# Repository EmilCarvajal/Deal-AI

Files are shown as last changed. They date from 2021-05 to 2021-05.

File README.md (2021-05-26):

# [ROBOTICA] Deal-AI
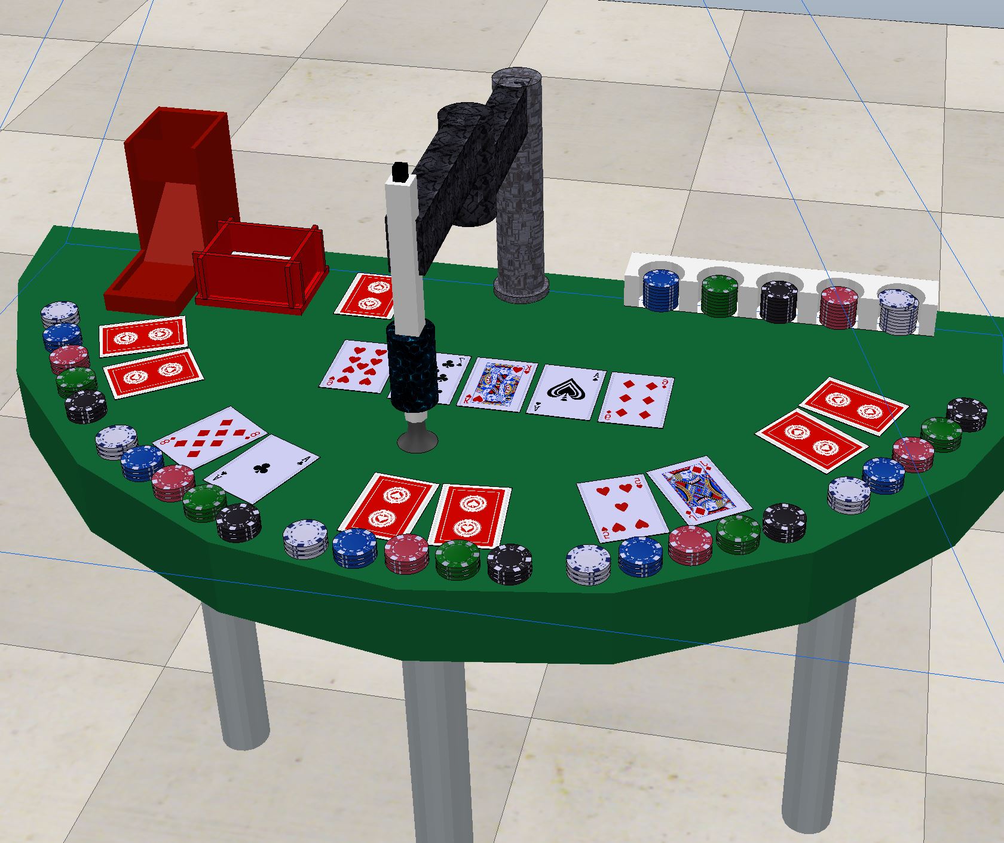
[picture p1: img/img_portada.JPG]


Brazo mecánico que  permite actuar como  Dealer o Croupier en el juego del  Poker, concretamente la modalidad de Texas Holdem.
También ayuda a controlar el estado de la partida.

# Tabla de Contenidos
* [Descripción de proyecto](#descripción-del-proyecto)

* [Amazing contributions](#amazing-contributions)

* [Esquema Hardware](#esquema-hardware)	

* [Piezas 3D](#piezas-3d)

* [Arquitectura software](#arquitectura-software)

* [Módulos](#módulos)
  * [Módulo de Jugadores](#módulo-de-jugadores)  <br>
  * [Módulo de cinemática inversa](#módulo-de-cinemática-inversa)  <br>
  * [Módulo de visión por computador](#módulo-de-visión-por-computador)  <br> 
       * [Detección de cartas](#detección-de-cartas)  <br>
       * [Detección de fichas](#detección-de-fichas)  <br>
  * [Módulo de inteligencia artificial](#módulo-de-inteligencia-artificial) <br>
       * [Main](#main) <br>
       * [Módulo de cambio](#módulo-de-cambio) <br>
* [Vídeo](#vídeo)

* [Autores](#autores)

# Descripción del proyecto	
DEAL_AI es un robot que ayuda a dirigir el estado de una partida del clásico juego de cartas Poker actuando como Dealer o Croupier.
Básicamente consiste en un brazo mecánico de 4 ejes con la misma estructura de un robot SCARA que tiene acoplada una ventosa para poder distribuir las fichas y las cartas que están en juego. Este robot está diseñado para una mesa semicircular la cual está adaptada a su zona de trabajo.  Existe un componente situado al lado de la base el cual le permite girar las cartas simplemente soltándolas por encima del objeto. Para reconocer las fichas y las cartas tiene una cámara colocada en una torre central elevada.
Sus principales funciones son:
*	Funciones de Dealer: 
       *	Flop (mostrar las 3 cartas)
       * Mostar las 5 cartas
       * Voltear cartas
       *	Repartir cartas 
*	Intercambio de fichas mediante IA
*	Realizar movimientos y responder preguntas (órdenes captadas por reconocimiento de voz)
* Declarar ganador por medio de visión por computador.

# Amazing contributions
Gracias a su adaptación para permitir cualquier número de jugadores, DEAL_AI puede ser utilizado en partidas amateurs o en partidas profesionales.
En cuanto a las partidas amistosas o hechas por principiantes, el robot permite a los jugadores tener una mayor comprensión del juego gracias a su seguimiento por comandos de voz y a su automatización en el intercambio de fichas. 
Para los jugadores profesionales, es ideal tener un crupier robótico, pues uno de los mayores problemas en el póker es la realización de [trampas](https://www.pokernews.com/news/2020/05/the-muck-bill-perkins-dan-cates-alleged-cheating-37330.htm) en medio de la partida. Se han dado casos donde el jugador que repartía cartas (en caso de no haber crupier) realizaba trampas para manipular las cartas que recibía cada jugador y, en otras ocasiones, un jugador estaba [compinchado con el crupier](https://www.straitstimes.com/singapore/courts-crime/rws-casino-croupier-and-patron-charged-with-cheating), por tanto este manipulaba las cartas que repartía a cada jugador.
Además, gracias a su movilidad automatizada y adaptable a las circunstancias de la partida, DEAL_AI tiene acceso a todos los rincones de la zona de juego, así pues en mesas grandes donde un jugador debe realizar un esfurezo físico para alcanzar la zona, lo que puede suponer un problema sobretodo para gente mayor, con discapacidad o problemas físicos, el robot es capaz de alcanzar las cartas y las fichas de cada jugador, ahorrandoles este esfuerzo inecesario para disfrutar de la partida de póker.

# Esquema Hardware
El proyecto en cuestión roza los 100€ de presupuesto con componentes de media calidad. Es necesario que 3 de los servo-motores sean capaces de realizar una rotación de 360º. Cabe destacar que, cuanto mayor sea la definición de la cámara, más se reducirá la tasa de error del robot al realizar la detección de fichas y, sobretodo, de cartas: Recomendamos una cámara capaz de grabar en Full HD.

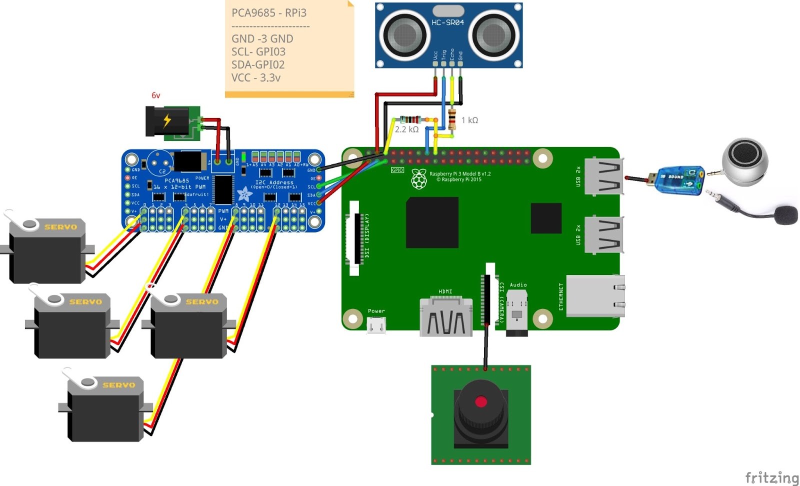
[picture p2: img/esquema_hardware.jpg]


# Piezas 3D
Para la realización de este proyecto, se han utilizado las siguientes piezas 3D:

**Componentes unidos del brazo robótico (total de 4 piezas por separado).**
<br>
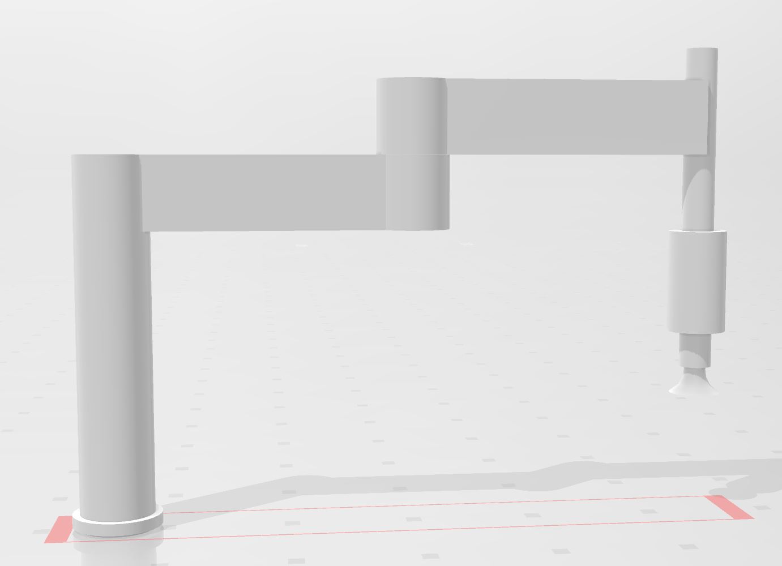
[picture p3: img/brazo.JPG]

<br>
<br>

**Base personalizada para colocar la baraja de cartas.**
<br>
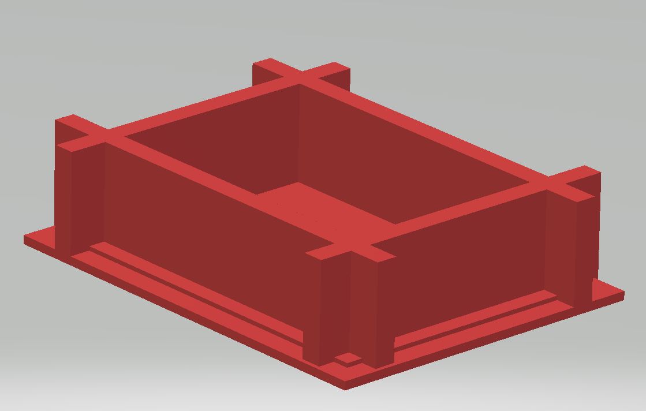
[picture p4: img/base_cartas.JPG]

<br>
<br>

**Pieza que permite al robot voltear las cartas.**
<br>
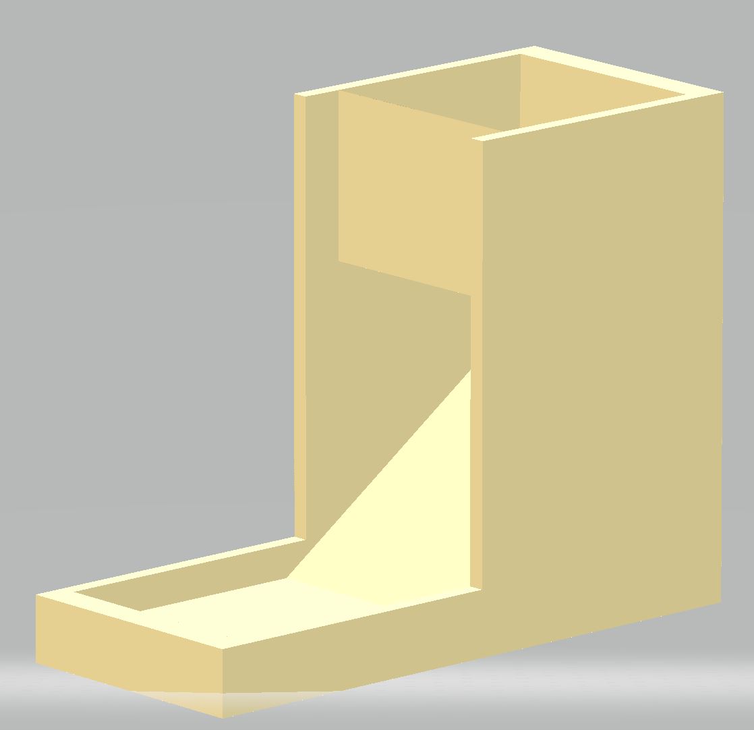
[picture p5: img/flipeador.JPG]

<br>
<br>

**Mesa semicircular utilizada en el simulador como zona de juego (no se ha de imprimir en caso de realizarlo en la vida real).**
<br>
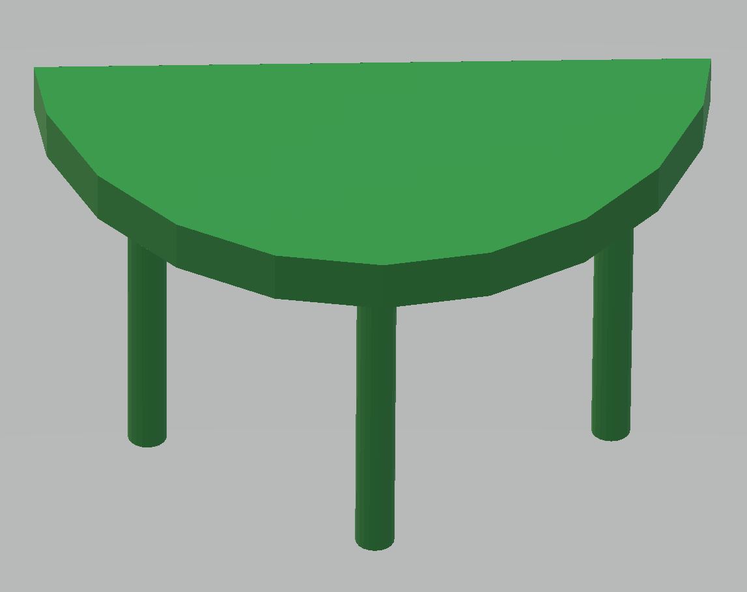
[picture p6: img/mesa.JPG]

<br>
<br>
Todas y cada una de estas piezas se encuentran en la carpeta **Objetos STL** de este mismo repositorio. No obstante, las dimensiones de los objetos NO SON CORRECTAS, simplemente conservan las buenas proporciones y relaciones de tamaño, pero en caso de querer utilizarlos se ha de tener en cuenta que se han de escalar al tamaño deseado. En nuestro caso, al utilizar un simulador y trasladarlo todo a centímetros (por temas de capacidad de ejecución y limitación de los própios ordenadores), se han escalado la gran mayoría de piezas a un ratio de entre 0.001 y 0.01 de su tamaño original.

# Arquitectura software
Destacamos un total de 4 módulos imprescindibles en este proyecto los cuales, al sincronizarse, permiten al robot realizar un seguimiento eficiente de la partida de póker que se esté llevando a cabo. Dichos módulos son:
* Módulo de jugadores: Reconocimiento de comandos de voz (inputs) que permiten al robot poder avanzar en la partida o la acción a realizar en cada momento. También permite a los jugadores consultar dudas básicas que tengan.
* Módulo de cinemática inversa: Movimiento absoluto del robot, ya sea para repartir cartas, intercambiar fichas o dar la vuelta a las cartas. Este módulo en particular también permite la reorientación correcta de las cartas.
* Módulo de visión por computador: Reconocimiento de fichas y cartas. Es capaz de detectar el valor de las fichas estándar de póker (colores blanco, azul, verde, rojo, negro) y el valor y palo de las cartas.
* Módulo de inteligencia artificial: Representa el cerebro del robot, el cual recibe los inputs de los demás módulos y genera los outputs que necesitan los demás módulos.
* Controladores: Estos relacionan los demás módulos entre si y permiten una perfecta sincronización entre ellos para poder efectuar las acciones necesarias.

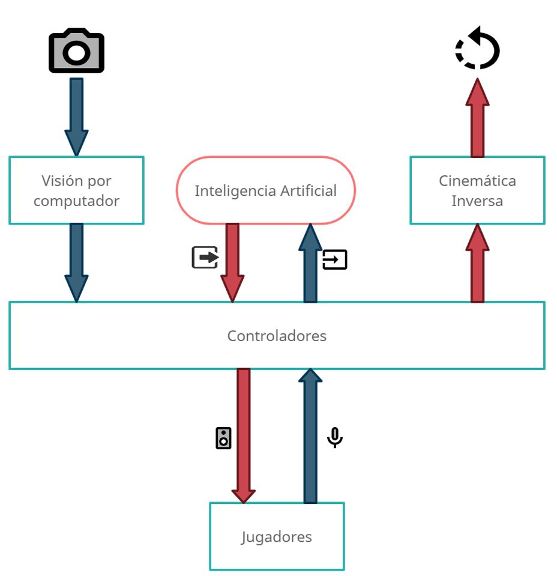
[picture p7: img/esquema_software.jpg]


# Módulos
## Módulo de jugadores
Representa el colectivo de seres humanos que están realizando una partida con el Deal AI. Estos son los que generarán los inputs principales, los cuales permitirán determinar al robot qué algoritmo utilizar y con qué módulos operar.

Para poder permitir esta interacción entre el boto y los jugadores, se han utilizado los módulos/librerías:
* speech_recognition (para el reconocimiento de voz, así dando la oportunidad de controlar las acciones del robot). 
> pip install SpeechRecognition
* gTTS (para poder leer con voz sintética (text-to-speech) las respuestas dadas por el robot)
> pip install gTTS
* playsound (para poder reproducir sonidos y poder leer los resultados obtenidos por el gTTS).
> pip install playsound

## Módulo de cinemática inversa
En este módulo se aplicará a los servo-motores los ángulos calculados para permitir al robot alcanzar el objeto o la posición deseada rotando sus ejes principales. Básicamente tras haber establecido la posición (módulo IA) el controlador ordenará a los componentes hardware la cinemática a realizar.

Lo principal para poder empezar a desplazar nuestro robot hacia las posiciones deseadas, es calcular las ecuaciones de movimiento del robot mediante una tabla de Denavit Hartenberg (tabla de D-H).

Para ello, hacemos los correspondientes cálculos en función de la diferencia entre las distancias y orientaciones de un servo-motor y otro. Al aplicar los cálculos correctos, obtenemos la siguiente matriz resultante para el cálculo de la cinemática inversa de un robot SCARA de 4 ejes:  

header pic

En esta ecuación conocemos los valores de la, lb, lc y l4 que equivalen a la distancia de cada brazo o link. Los datos que desconocemos son ϑ1, ϑ2, ϑ4 y d3, que equivaldrían a los ángulos de rotación de los servo-motores 1, 2 y 4 (los cuales son rotacionales) y la altura a la que está situada el manipulador (controlado por el servo-motor 3 que es de tipo prismático). Para saber qué rotación hay que aplicar a cada eje, utilizamos la última columna para realizar un sistema de ecuaciones que, al resolverlo, nos determinará las rotaciones a aplicar en cada eje. No obstante, si queremos saber la rotación correspondiente para punto geométrico (x, y, z), debemos restar estos valores a su ecuación correspondiente (la primera fila corresponde a la 'x', la segunda a la 'y' y la tercera a la 'z').

En nuestro caso utilizamos la librería sympy.
> import sympy as sp  
> from sympy import *

Dicha librería nos permite obtener una representación más visual de las ecuaciones y utilizar funciones de resolución de sistemas de ecuaciones para encontrar las incógnitas. En nuestro caso, mediante la matriz de DH mostrada previamente:
> nsolve(matrix, (theta1,theta2,d3,theta4),(1, 1, 1, 1))

Para facilitar la faena de los programadores, se crean módulos estándar que serán utilizados en las funciones principales, así pues, para repartir cartas a un jugador, en vez de reescribir el código de cinemática inversa, se utiliza un módulo de movimiento estándar que es llamado por la función de mayor nivel.

Con este sistema establecido, generamos las siguientes funciones de alto nivel:

*	**PosicionJugador(nJugadores):** Se pasa como parámetro ‘nJugadores’ que corresponde al número de participantes que jugarán a póker. La función calcula y devuelve las posiciones geométricas de cada jugador y el ángulo correspondiente (entre 90 y -90 grados porque es una mesa semicircular y el robot está orientado en el ángulo 0 grados).

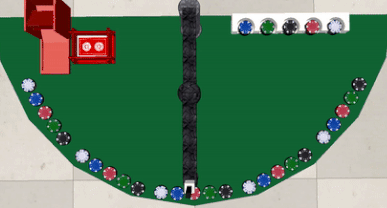
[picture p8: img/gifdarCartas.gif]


*	**DarCartaJugador(x, y, angulo):** Se pasa como parámetro la posición central de un jugador. En esta función se le suma y resta a esta posición un coeficiente pequeño que determina la separación entre una carta y otra, pues en esta modalidad de póker ser reparten dos cartas a cada jugador. Una vez aplicado este cálculo, se determina de la posición central un total de 2 posiciones, que equivalen a las posiciones de cada carta. Puesto que se colocan las cartas de los jugadores en el perímetro del área, al colocar el eje rotacional en el ángulo 0 grados, las cartas quedan orientadas apuntando hacia el centro de la mesa.

*	**RevelarCartasCentrales():** En esta función se revelan las cartas correspondientes cuando da inicio una nueva ronda. En esta modalidad de póker, se revelan un total de 5 cartas: 3 cartas en la primera ronda, 1 carta en la segunda y 1 carta en la tercera.

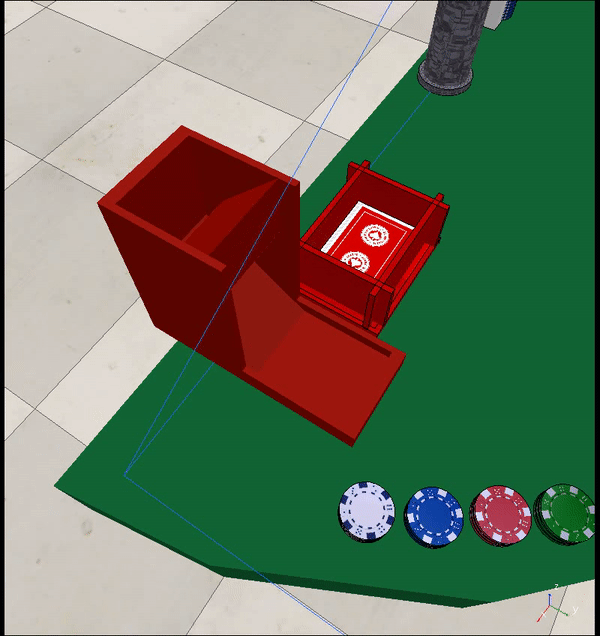
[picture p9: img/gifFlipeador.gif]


* **Ir_a_flipeador():** Tras analizar y probar varios modelos de piezas 3D que permitan voltear una carta automáticamente, hemos encontrado la pieza necesaria para lograrlo. Tras situar la pieza en un lugar específico de la zona de juego, el brazo robótico únicamente debe colocar encima de la pieza la carta que desea voltear, rotando dicha carta para que quepa en la entrada y se voltee automáticamente, deslizándose hasta una pequeña zona donde se recogerá la carta.

*	**QuemarCarta():** En muchos juegos de cartas de apuestas antes de repartir cartas o de revelar cartas se realiza una acción denominada como “quemar carta” que simplemente consta en coger la primera carta del mazo y colocarla en una pila de descartes.

**Problema 1:** La función ‘nsolve’ muestra problemas para encontrar el camino óptimo que ha de recorrer el robot y, en ciertas ocasiones para llegar a la coordenada de destino realiza más vueltas de las necesarias (gira más de 360 grados).

**Solución 1:** En el módulo del cálculo de la cinemática inversa se aplica el módulo a la solución para así obtener un resultado entre 0 y 360 grados:

> angulo=angulo % 2π

En este caso, ‘angulo’ es el parámetro que nos devuelve la función ‘nsolve’ que equivaldría a la rotación que debería ejercer el servo-motor para alcanzar la coordenada en cuestión. 2π equivale a 360 grados en radianes.

**Problema derivado 1.1:** La operación módulo (%) no tiene en cuenta el signo del ángulo, es decir, si la variable ‘angulo’ es positiva, el resultado será positivo, pero en caso de ser un valor negativo, el resultado que devuelve es positivo cosa que no nos interesa, pues hay una gran diferencia entre girar 45 y -45 grados.

**Solución 1.1:** Puesto que no hay ninguna función que permita realizar la operación de módulo devolviendo el signo correcto, se detecta el signo antes de aplicar la operación y, en caso de ser negativo, se calcula el módulo con el valor positivo y luego se negativiza el resultado.

**Problema derivado 1.2:** La variable ‘angulo’ ahora está comprendida entre 0 y 360 grados, pero en ciertas ocasiones el brazo gira casi 360 grados para acceder a una posición cercana si se desplazara en dirección contraria. Por ejemplo, si el robot quiere situarse en el centro del 4to cuadrante (cuadrante (x, -y) entre los ángulos 270 y 360) podría acceder de manera rápida si rotara -45 grados, pero la función nos devuelve un valor de 315, por tanto el brazo rota un total de 315 grados lo cual no es óptimo.

**Solución 1.2:** Los brazos robóticos con capacidad de rotación de 360 grados pueden dividirse en dos zonas de movimiento óptimo: de 0 a 180 grados y de 0 a -180 grados (que equivaldría a la zona comprendida entre 180 y 360 grados). Si el robot quiere rotar 181 grados, es más eficaz que rote -179 grados, pues llegará a la misma posición rotando menos grados. Por tanto, se determina un condicional que si detecta que la variable ‘angulo’ supera los 180 grados (que en radianes equivale a π), entonces se le resta 360 grados a ‘angulo’ (equivalente a 2π), así pues, en el mismo caso de antes, si tenemos 181 grados y le restamos 360, obtenemos -179 que sería nuestro ángulo óptimo.

**Solución final:** Juntando todas estas soluciones, obtenemos un módulo capaz de corregir cualquier ángulo y transformarlo en uno óptimo (si es que no lo era antes):

Cuanto a los módulos de bajo nivel, mencionamos algunos que creemos que son interesantes mencionar:
* **CogerItem():** Activa la válvula de vacío.
* **CogerCarta():** Automatiza la acción de coger una carta de la baraja (utilizando la función CogerItem()).
* **DejarItem():** Desactiva la válvula de vacío.

## Módulo de visión por computador:
Entendemos este módulo como el que recoge la información de la situación en la zona de juego. Dicha información se utilizará posteriormente para poder establecer las posiciones de los elementos a manipular por el robot (cartas y fichas) y para que pueda determinar la situación en tiempo real de la partida (reconocimiento de las cartas).

Finalmente, para este módulo se ha decidido hacerlo junto con el proyecto final de la asignatura “Visión por Computador”. El robot será capaz de detectar tanto cartas como fichas. Además de detectarlos podrá saber sus valores concretos.

### Detección de cartas
Se ha limitado una zona para cada jugador donde se encontrarán las cartas y fichas correspondientes de cada jugador. Se ha implementado una función llamada “**detectarCartes()**” que se le pasan por parámetro la región de la imagen del jugador recortada y otra igual pero binarizada (en blanco y negro) y la cantidad de cartas que se esperan que se detecten (2 si son la de los jugadores y 5 si son las de la máquina). Esta función se encarga de tractar las imágenes que recibe para devolver 3 vectores, el primero contiene una imagen de cada carta, el segundo una imagen del rango / valor de las cartas detectadas (A, 1, 2, 3, …, Q,K) y el tercero contiene una imagen del palo de cada carta detectada (corazón, picas, tréboles, rombos).  
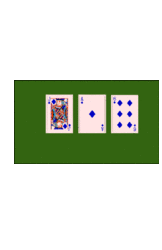
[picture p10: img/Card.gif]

También, se ha implementado una función llamada “**detectarValors()**” que recibe las imágenes de los valores y tipos obtenidos en la función “**detectarCartes()**” y un dataset de valores de cartas y un dataset de valores de palos de Póker. En esta función se usan los dataset que se pasan por parámetro para clasificar los palos y valores de cada una de las imágenes que también recibe y devolver 2 vectores en un formato específico para posteriormente determinar quién es el ganador.  
Para poder saber quién es el ganador, se ha implementado una función llamada “**comboJugador()**” que mediante los vectores que devuelve “**detectarValors()**” le da una puntuación al jugador sobre la mano que tiene y con qué combo (pareja, doble pareja, escalera, …) ha obtenido esa puntuación (el jugador que obtenga la mayor puntuación será el ganador).

### Detección de fichas
Para esta detección, no se utilizan las mismas zonas que para las cartas porque estas no coinciden con la zona natural donde un jugador podría dejar sus fichas (entendemos que un jugador no situaría las fichas que quiere cambiar encima de sus cartas sino un poco más alejado de ellas). Así pues, antes de que el robot las detecte, sume su valor y pueda recogerlas y llevarlas a la banca de fichas para su intercambio, lo primero que se ha realizar es determinar las áreas de cambio.  
Se ha creado la función "**valorFichas(img_Robot)**" que se encarga de determinar el valor de una ficha. Esta recibe una imagen de la área determinada por el jugador que pide cambio de fichas. La imagen contiene varias fichas, pero al estar apiladas solo ve la que está más por encima.
Los pasos que emplea son:
*	Eliminación del ruido 
*	Encuentra el área del fondo 
*	Encuentra el área segura que pertenece a la ficha
*	Encuentra la región desconocida (bordes)
*	Etiquetado de las manchas que detecta
*	Adiciona 1 a todas las etiquetas para asegurra que el fondo sea 1 en lugar de cero
*	Se marca la región desconocida con ceros
*	Utiliza técnica “watershed” para dividir las manchas
*	Se binariza la imagen
*	Buscamos los contornos las manchas restantes con la función cv2.findContours()
*	Recortamos la mancha
*	Le añadimos brillo mediante la función increase_brightness()
*	Realizamos una media de pixeles y vemos que color es más cercano para asociarle

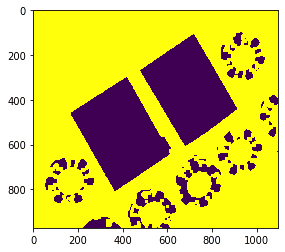
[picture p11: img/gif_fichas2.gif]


## Módulo de inteligencia artificial
### Main
Este es el núcleo del robot, donde todos los inputs son transmitidos a este módulo el cual se encargará de dar una serie de órdenes al robot. Estas órdenes pasarán por su controlador en concreto y establecerá una acción: o bien utilizará el altavoz para dar un mensaje a los jugadores o bien realizará un movimiento para alcanzar una posición calculada previamente.

Este main representa el sistema del juego Póker en la modalidad Texas Holdem pero con ciertos cambios que permiten que se adapte a una partida cotidiana entre amigos.
Por eso, cada jugador empieza con una cantidad de fichas determinadas. El sistema está organizado por “Manos” y “Rondas”. Denominamos Manos a 4 Rondas completas donde en la última se decide quién es el jugador que ha ganado la Mano y se lleva todo el dinero situado en el bote. Un Ronda es terminada cuando todos los jugadores activos de la Mano han apostado la misma cantidad de fichas. En la Ronda 0 se reparten las cartas y se realizan las apuestas iniciales, en la Ronda 1 se colocan 3 cartas centrales en la mesa y en la ronda 2 y 3 se “quema” una carta y se coloca otra junto a las centrales. “Quemar” una carta no es más que coger una carta y descartarla colocándola en una pila de descartes.
El sistema controla la secuencia de juego y mantiene el estado de los jugadores que no se han retirado para pasar a la siguiente ronda. 
Controla en todo momento los jugadores que están activos y los que han abandonado la mesa (no se contemplan para las siguientes Manos y no se les reparte cartas).

Cuando es el turno de un jugador se le pregunta, por comandos de voz, qué acción desea realizar. Solo se ejecutan las acciones que ordena si se encuentran en el sistema. Estas acciones son típicas del juego como:
*	<ins> “Paso”:</ins> el jugador no desea subir la apuesta.
*	<ins> “Subo”:</ins> el jugador sube la apuesta y se reinicia el estado de los jugadores para confirmar sus nuevas acciones.
*	<ins> “Igualo, Voy”:</ins>  el jugador sigue la apuesta máxima y coloca sus fichas en la mesa.
*	<ins> “Me retiro”:</ins> Se retira de la Mano y no se le preguntará nada hasta la próxima Mano.
*	<ins> “Abandono”:</ins> Abandona la mesa y ya no se le tendrá en cuenta en las próximas Manos.
*	<ins> “Cambio a la alta/baja”:</ins> El jugador coloca sus fichas en su área de cambio según si desea cambio a valores altos o bajos. Implementado por el Módulo de Cambio.
*	<ins> Preguntas de estado:</ins>  Se le puede preguntar al sistema información sobre el estado del juego. Ej: “Dealer actual?”, “Ronda actual?, “Quién es la ciega grande?”, “Apuesta máxima?”… 

Cuando se ha llegado a la última Ronda de una Mano el sistema dice a los jugadores que han permanecido al final de la Mano que muestren sus cartas. 
El sistema reconoce todas las cartas que hay en la mesa gracias al módulo de visión por computador y determina el jugador que ha ganado y la combinación de cartas con lo que lo ha hecho. 

Para las siguientes Manos el sistema de juego es el mismo. Se termina el juego cuando solo queda un jugador en la mesa.

### Módulo de cambio
Este módulo controla el sistema de cambio de fichas. Se implementa en 3 etapas: reconocimiento de las fichas que se desean cambiar y llevarlas a la banca, tratamiento del valor total de las fichas para establecer cuantas monedas y de qué tipo ha de devolver y por último la secuencia de movimientos para colocar las fichas de cambio.

Funciones:
*	**recogerFichasMonton(area):** Por medio de un área establecida controla el módulo de visión por computador de las fichas para poder reconocerlas y luego a través de las funciones de cinemática inversa coloca esas fichas en su determinada posición de la banca.

*	**cambiar_fichas_greedy(suma_fichas,mode):** Algoritmo greedy (sacado  de la asignatura de la mención “Analisis y disseny d’algortimes” ) implementado para saber qué fichas ha de devolver el robot. Implementa 2 modos para devolver fichas con valores bajos o máximos.

*	**dar_Cambio(cambio, posicion):** Recibe qué fichas se han de devolver y la matriz de la posición donde el jugador dejó sus fichas de cambio.

# Vídeo
Haz click para ver el video:
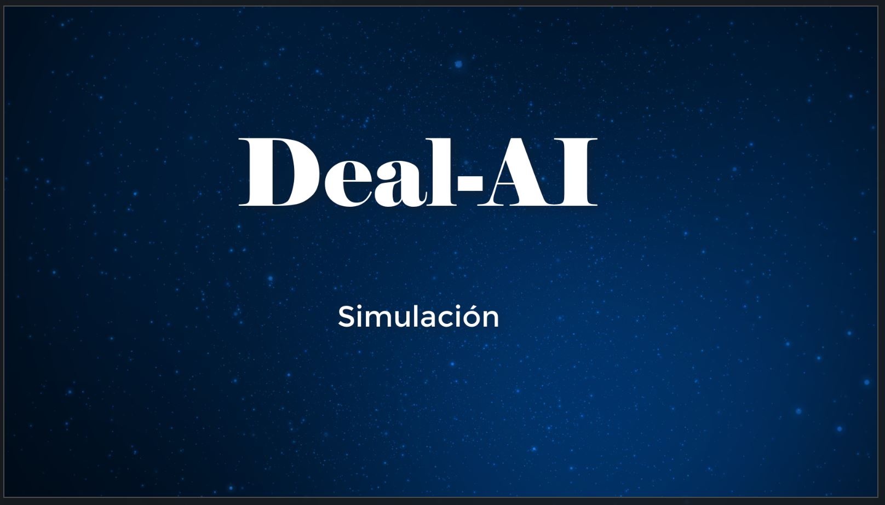
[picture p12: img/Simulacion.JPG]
Watch the video (https://www.youtube.com/watch?v=U3uC58L_5Mo&ab_channel=Emilsj2)


# Autores
Emil Carvajal - 1529821   
Marc Gordón - 1457460   
Jofre Gómez - 1526889   
Denís Montoya - 1527418

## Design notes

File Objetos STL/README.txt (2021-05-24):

Los objetos siguen las proporciones adecuadas, pero NO ESTÁN ESCALADOS al 
tamaño correcto, por tanto consultar proporciones si se quieren implementar.

Objetos como las cartas o las fichas son para representar la forma, el valor
de cada uno se representará después individualmente. En caso de usar Coppelia
se aplicará una 'Quick Texture' para añadir el valor de la ficha o de la carta.

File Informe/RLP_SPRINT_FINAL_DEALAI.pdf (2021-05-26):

RPL - Computer Engineering. UAB (Barcelona) 2020-2021

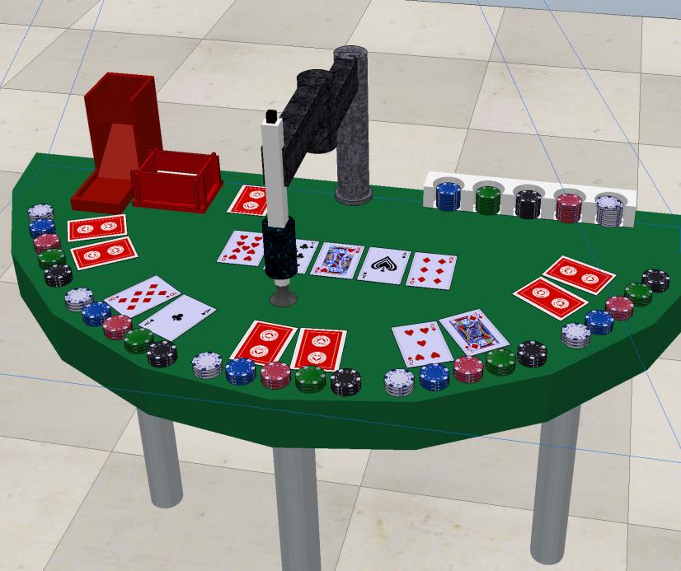
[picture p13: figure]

# DEAL_AI

Brazo | mecánico | que | permite actuar como
Dealer o Croupier | en | el | juego del | Poker,
concretamente la modalidad de Texas Holdem. También ayuda a controlar el estado de la partida.

PROJECT SPRINT #5.
DATE: 25th May 2021

EMIL CARVAJAL 1529821 #1
DENÍS MONTOYA 1527418 #2
MARC GORDÓN 1457460 #3
JOFRE GÓMEZ 1526889 #4

DEAL_AI

## Tabla de contenido

Sprint #5
Date: 25 Mayo 2021
DEAL_AI | 1

## DEAL_AI

Brazo mecánico que permite actuar como Dealer o Croupier en el juego del Poker, concretamente la modalidad de Texas Holdem. También ayuda a controlar el estado de la partida.

Descripción del Proyecto

DEAL_AI es un robot que ayuda a dirigir el estado de una partida del clásico juego de cartas Poker actuando como Dealer o Croupier.

Básicamente consiste en un brazo mecánico de 4 ejes con la misma estructura de un robot SCARA que tiene acoplada una ventosa para poder distribuir las fichas y las cartas que están en juego. Este robot está diseñado para una mesa semicircular la cual está adaptada a su zona de trabajo. Existe un componente situado al lado de la base el cual le permite girar las cartas simplemente soltándolas por encima del objeto. Para reconocer las fichas y las cartas tiene una cámara colocada en una torre central elevada.

Sus principales funciones son:

- Funciones de Dealer:
- Flop (mostrar las 3 cartas)
- Mostar las 5 cartas
- Quemar cartas
- Incluye voltear las cartas
- Repartir Cartas
- Intercambio de fichas mediante IA
- Realizar movimientos y responder preguntas (órdenes captadas por reconocimiento de voz)
- Declarar ganador por medio de visión por computador.

DEAL_AI | 2

Componentes electrónicos

■ Placa PCA9685

■ Raspberry pi 3

■ 4 Servomotores

■ Cámara

■ Adaptador de audio

■ Micrófono

■ Altavoz

■ Ventosa de bomba de aire de vacío

■ 5 sensores de ultrasonido

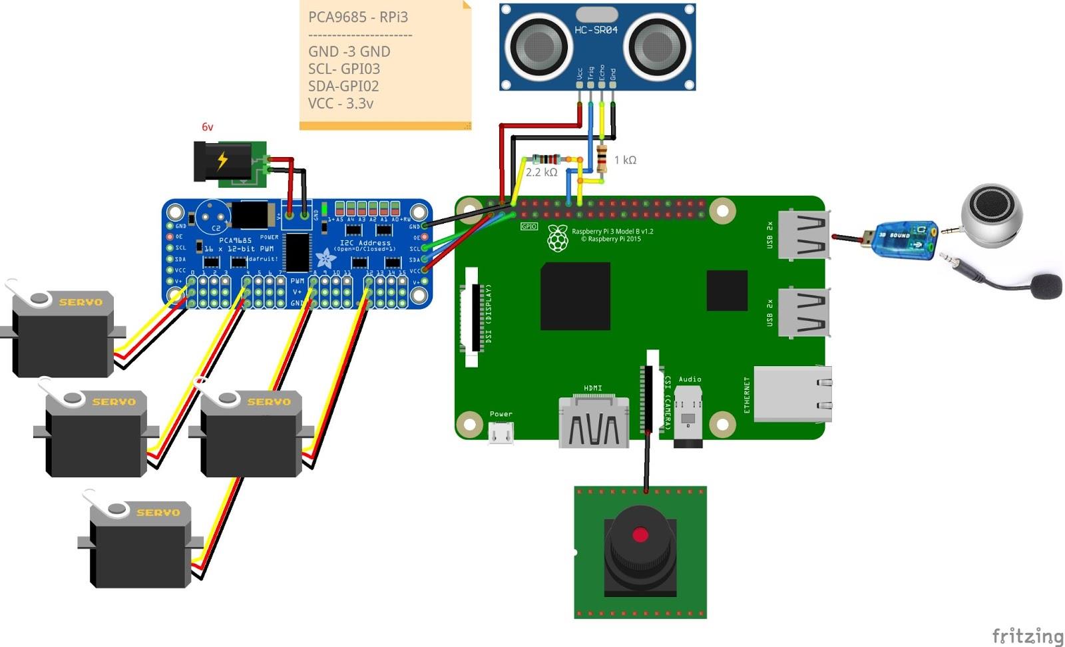
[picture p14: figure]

DEAL_AI | 3

Esquema Hardware

CONEXIONES (--> Serie // Paralelo)

SERVO1,2,3,4 (pin,v,gnd) --> PCA9685 ( (0,4,8,12 ) , 5v, GND) )

PCA9685 (Vin,GND,SCL,SDA) --> Raspberry pi 3 (5v, GND, GIPO03,GIPO04)

Raspberry pi 3 (CSI camera) --> Camera

Raspberry pi 3 ( USB1 port) --> Adaptador de Audio

Adaptador de Audio( in ) --> External Microphone

Adaptador de Audio( out ) --> External Speaker

HC - SR04 (Vcc,GND,Trig,Echo) --> Raspberry pi 3 (5v, GND, (GND,GIPO23), GIPO24)

- | HC - SR04 (Trig) --> R1(1kΩ) --> | Raspberry pi 3(GIPO24)
// R2(2.2kΩ) --> | Raspberry pi 3(GND)

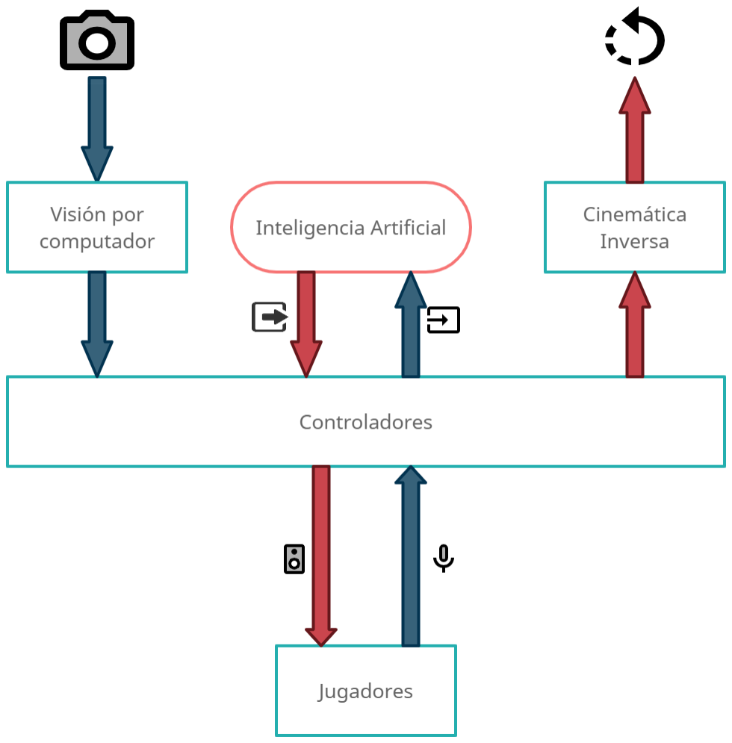
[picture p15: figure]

DEAL_AI | 4

Arquitectura Software

DEAL_AI | 5

Visión por computador:

Entendemos este módulo como el que recoge la información de la situación en la zona de juego. Dicha información se utilizará posteriormente para poder establecer las posiciones de los elementos a manipular por el robot (cartas y fichas) y para que pueda determinar la situación en tiempo real de la partida (reconocimiento de las cartas).

Finalmente, para este módulo se ha decidido hacerlo junto con el proyecto final de la asignatura “Visión por Computador”. El robot será capaz de detectar tanto cartas como fichas. Además de detectarlos podrá saber sus valores concretos.

Para la detección de cartas, se ha limitado una zona para cada jugador conde se encontrarán las cartas y fichas correspondientes de cada jugador.
Se ha implementado una función llamada “detectarCartes” que se le pasan por parámetro la región de la imagen del jugador recortada y otra igual pero binarizada (en blanco y negro) y la cantidad de cartas que se esperan que se detecten (2 si son la de los jugadores y 5 si son las de la máquina). Esta función se encarga de tractar las imágenes que recibe para devolver 3 arrays, el 1º contiene una imagen de cada carta, el 2º una imagen del rango / valor de las cartas detectadas (A, 1, 2, 3, …, Q,K) y el 3º contiene una imagen del palo de cada carta detectada (corazón, picas, tréboles, rombos).
También, se ha implementado una función llamada “detectarValors” que recibe las imágenes de los valores y tipos obtenidos en la función “detectarCartes” y un dataset de valores de cartas y un dataset de valores de palos de Poker. En esta función se usan los dataset que se pasan por parámetro para clasificar los palos y valores de cada una de las imágenes que también recibe y devolver 2 arrays en un formato específico para posteriormente determinar quien es el ganador. Para poder saber quien es el ganador, se ha implementado una función llamada “comboJugador” que mediante los arrays que devuelve “detectarValors” le da una puntuación al jugador sobre la mano que tiene y con que combo (pareja, doble pareja, escalera, …) ha obtenido esa puntuación (el jugador que obtenga la mayor puntuación será el ganador).

DEAL_AI | 6

Para la detección de las fichas no se utilizan las mismas zonas que para las cartas porques estas no son usadas ya que no contienen el area donde el jugador puede dejar sus fichas para que el robot las detecte, sume su valor y pueda recogerlas y llevarlas a la banca de fichas para su intercambio. Por lo que lo primero ha sido determinar esas áreas de cambio

valorFichas(img_Robot): Función que se encarga de determinar el valor de una ficha. Esta recibe una imagen de la área determinada por el jugador que pide cambio de fichas. La imagen contiene varias fichas, pero al estar apiladas solo ve la que está más por encima.

Los pasos que emplea son:

- Eliminación del ruido
- Encuentra el área del fondo
- Encuentra el área segura que pertenece a la ficha
- Encuentra la región desconocida (bordes)
- Etiquetado de las manchas que detecta
- Adiciona 1 a todas las etiquetas para asegurra que el fondo sea 1 en lugar de cero
- Se marca la región desconocida con ceros
- Utiliza técnica “watershed” para dividir las manchas
- Se binariza la imagen
- Buscamos los contornos las manchas restantes con la función cv2.findContours()
- Recortamos la mancha
- Le añadimos brillo mediante la función increase_brightness()
- Realizamos una media de pixeles y vemos que color es más cercano para asociarle

### Cinemática inversa:

En este módulo se aplicará a los servo motores la cinemática inversa calculada para permitir al robot alcanzar el objeto o la posición deseada. Básicamente tras haber establecido la posición (módulo IA) el controlador ordenará a los componentes hardware la cinemática a realizar.

Lo principal para poder empezar a desplazar nuestro robot hacia las posiciones deseadas, es calcular las ecuaciones de movimiento del robot mediante una tabla de Denavit Hartenberg (tabla de D-H).

Para ello, hacemos los correspondientes cálculos en función de la diferencia entre las distancias y orientaciones de un servo-motor y otro. Al aplicar los cálculos correctos, obtenemos la siguiente matriz resultante para la cinemática inversa de un robot SCARA de 4 ejes:

En esta ecuación conocemos los valores de la, lb, lc y l4 que equivalen a la distancia de cada brazo o link. Los datos que desconocemos son ϑ1, ϑ2, ϑ4 y d3, que equivaldrían a los ángulos de rotación de los servo-motores 1, 2 y 4 (los cuales son rotacionales) y la altura a la que está situada el manipulador (controlado por el servo-motor 3 que es de tipo prismático). Así pues, programamos un módulo básico para el cálculo de estas coordenadas:

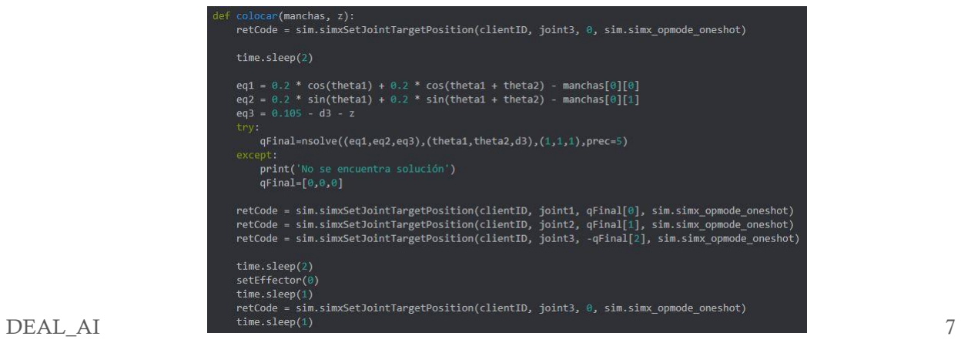
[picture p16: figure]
DEAL_AI

DEAL_AI | 8

Se utiliza el módulo base de la función “colocar” para ejercer toda la cinemática del robot. El núcleo de esta es la función “nsolve” que encontrar las incógnitas de un sistema de ecuaciones. Tanto las incógnitas como las ecuaciones se pasan como parámetros. En nuestro caso, se pasa como ecuaciones los resultados de aplicar la tabla D-H en un robot de 4 ejes SCARA y, para el movimiento, se encuentran los ángulos de los ejes rotacionales de los 2 primeros servo-motores. La altura no obstante será determinada mediante un sensor de ultrasonido, capaz de determinar la distancia a la que se encuentra la válvula de vacío (manipulador del robot) del objeto en cuestión (cartas o fichas).

Problema: La orientación del robot no es la predefinida, el robot está orientado en el eje de ordenadas en vez del de abscisas.

Solución: Se invierten los ejes en el cálculo de la posición, así pues, nuestras coordenadas realmente son (y, x).

Para facilitar la faena de los programadores, se crean módulos estándar que serán utilizados en las funciones principales, así pues, para repartir cartas a un jugador, en vez de reescribir el código de la cinemática inversa, se utiliza un módulo de movimiento estándar que es llamado por la función de mayor nivel.

Solución: Al utilizar un sistema de jerarquía de funciones, podemos volver a trabajar con el sistema de coordenadas (x,y) en general, hemos realizado el cambio a (y,x) en la función de menor nivel pero nos permite trabajar de manera normal y cómoda de esta forma.

Con este sistema establecido, generamos las siguientes funciones de alto nivel:

- PosicionJugador(nJugadores): | Se | pasa | como | parámetro
‘nJugadores’ que corresponde al número de participantes que jugarán a póker. La función calcula y devuelve las posiciones geométricas de cada jugador y el ángulo correspondiente (entre 90 y -90 grados porque es una mesa semicircular y el robot está orientado en el ángulo 0 grados).

DEAL_AI | 9
- DarCartaJugador(x, y, angulo): Se pasa como parámetro la posición central de un jugador. En esta función se le suma y resta a esta posición un coeficiente pequeño que determina la separación entre una carta y otra, pues en esta modalidad de póker ser reparten dos cartas a cada jugador. Una vez aplicado este cálculo, se determina de la posición central un total de 2 posiciones, que equivalen a las posiciones de cada carta. Puesto que se colocan las cartas de los jugadores en el perímetro del área, al colocar el eje rotacional en el ángulo 0 grados, las cartas quedan orientadas apuntando hacia el centro de la mesa.
- RevelarCartasCentrales(): En esta función se revelan las cartas correspondientes cuando da inicio una nueva ronda. En esta modalidad de póker, se revelan un total de 5 cartas: 3 cartas en la primera ronda, 1 carta en la segunda y 1 carta en la tercera.
- Ir_a_flipeador(): Tras analizar y probar varios modelos de piezas 3D que permitan voltear una carta automáticamente, hemos encontrado la pieza necesaria para lograrlo. Tras situar la pieza en un lugar específico de la zona de juego, el brazo robótico únicamente debe colocar encima de la pieza la carta que desea voltear, rotando dicha carta para que quepa en la entrada y se voltee automáticamente, deslizándose hasta una pequeña zona donde se recogerá la carta.

Problema: El brazo no es capaz de elevarse lo suficientemente alto como para colocar la carta en la parte superior de la pieza 3D.

Solución: Se han modificado las distintas dimensiones del robot, en concreto se ha incrementado la altura de la base del robot y se ha elevado el eje prismático, permitiéndonos depositar la carta en la parte superior del volteador.

Problema derivado: En algunos casos, para repartir las cartas a algunos jugadores, el brazo colisiona con el volteador de cartas, bloqueando el único medio de acceso hacia la posición del jugador.

Solución: Se ha modificado la función de nivel bajo CogerCarta() la cual, al recoger la carta de la baraja, la eleva lo máximo posible.

DEAL_AI | 10

De este modo, cada vez que se quiere acceder a una posición problemática, el brazo robótico se desplazará por encima de la pieza 3D, evitando colisiones innecesarias y permitiendo alcanzar cualquier posición sin impedimentos .

- QuemarCarta(): En muchos juegos de cartas de apuestas antes de repartir cartas o de revelar cartas se realiza una acción denominada como “quemar carta” que simplemente consta en coger la primera carta del mazo y colocarla en una pila de descartes.

Problema 1: La función ‘nsolve’ muestra problemas para encontrar el camino óptimo que ha de recorrer el robot y, en ciertas ocasiones para llegar a la coordenada de destino realiza más vueltas de las necesarias (gira más de 360 grados).

Solución 1: En el módulo del cálculo de la cinemática inversa se aplica el módulo a la solución para así obtener un resultado entre 0 y 360 grados:

angulo = angulo % 2π

En este caso, ‘angulo’ es el parámetro que nos devuelve la función ‘nsolve’ que equivaldría a la rotación que debería ejercer el servo-motor para alcanzar la coordenada en cuestión. 2π equivale a 360 grados en radianes.

Problema derivado 1.1: La operación módulo (%) no tiene en cuenta el signo del ángulo, es decir, si la variable ‘angulo’ es positiva, el resultado será positivo, pero en caso de ser un valor negativo, el resultado que devuelve es positivo cosa que no nos interesa, pues hay una gran diferencia entre girar 45 y -45 grados.

Solución 1.1: Puesto que no hay ninguna función que permita realizar la operación de módulo devolviendo el signo correcto, se detecta el signo antes de aplicar la operación y, en caso de ser negativo, se calcula el módulo con el valor positivo y luego se negativiza el resultado.

Problema derivado 1.2: La variable ‘angulo’ ahora está comprendida entre 0 y 360 grados, pero en ciertas ocasiones el brazo gira casi 360 grados para acceder

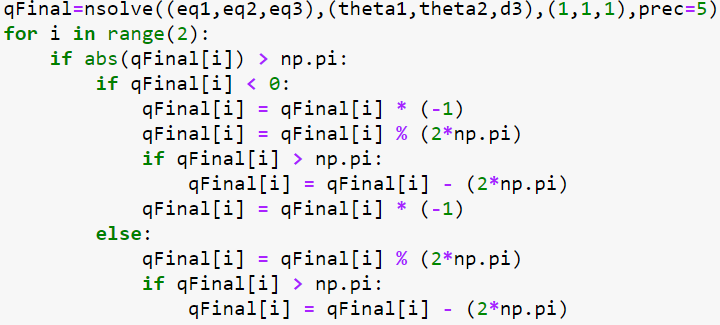
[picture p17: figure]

DEAL_AI | 11

a una posición cercana si se desplazara en dirección contraria. Por ejemplo, si el robot quiere situarse en el centro del 4to cuadrante (cuadrante (x, -y) entre los ángulos 270 y 360) podría acceder de manera rápida si rotara -45 grados, pero la función nos devuelve un valor de 315, por tanto, el brazo rota un total de 315 grados lo cual no es óptimo.

Solución 1.2: Los brazos robóticos con capacidad de rotación de 360 grados pueden dividirse en dos zonas de movimiento óptimo: de 0 a 180 grados y de 0 a -180 grados (que equivaldría a la zona comprendida entre 180 y 360 grados). Si el robot quiere rotar 181 grados, es más eficaz que rote -179 grados, pues llegará a la misma posición rotando una cantidad más pequeña de grados. Por tanto, se determina un condicional que si detecta que la variable ‘angulo’ supera los 180 grados (que en radianes equivale a π), entonces se le resta 360 grados a ‘angulo’ (equivalente a 2π), así pues, con el mismo caso de antes, si tenemos 181 grados y le restamos 360, obtenemos -179 que sería nuestro recorrido óptimo.

Solución final: Juntando todas estas soluciones, obtenemos un módulo capaz de corregir cualquier ángulo y transformarlo en uno óptimo (si es que no lo era antes):

Ejemplos de módulos de bajo nivel sería CogerItem() que activa la válvula de vacío, CogerCarta() que automatiza la acción de coger una carta de la baraja (utilizando la función CogerItem() ), DejarItem() que desactiva la válvula de

DEAL_AI | 12

vacío… En general son funciones sencillas que son llamadas varias veces por los módulos de alto nivel.

DEAL_AI | 13

Inteligencia Artificial:

Main:

Este es el núcleo del robot, donde todos los inputs son transmitidos a este módulo el cual se encargará de dar una serie de órdenes al robot. Estas órdenes pasarán por el controlador en concreto y establecerá una acción: o bien utilizará el altavoz para dar un mensaje a los jugadores o bien realizará un movimiento para alcanzar una posición calculada previamente.

Este main representa el sistema del juego Poker en la modalidad Holdem Texas pero con ciertos cambios que se adaptan a una partida cotidiana entre amigos. Por eso, cada jugador empieza con una cantidad de fichas determinadas. El sistema esta organizado por “Manos” y “Rondas”. Denominamos Manos a 4 Rondas completas donde en la última se decide quien es el jugador que ha ganado la Mano y se lleva todo el dinero invertido. Una Ronda es terminada cuando todos los jugadores activos de la Mano han apostado la misma cantidad de fichas. En la Ronda 0 se reparten las cartas, en la Ronda 1 se colocan 3 cartas centrales en la mesa y en la Ronda 2 i 3 se “quema” una carta y se coloca otra junto a las centrales. “Quemar” una carta no es más que coger una carta y descartar-la colocándola en una posición de la mesa.

El sistema controla la secuencia de juego y mantiene un estado de los jugadores que no se han retirado para pasar a la siguiente ronda.
Controla en todo momento los jugadores que están activos y los que han abandonado la mesa (no se contemplan para las siguientes Manos y no se les reparte cartas).

Cuando es el turno de un jugador se le pregunta, por comandos de voz, què acción desea realizar. Solo se ejecutan las acciones que ordena si se encuentran en el sistema. Estas acciones son típicas del juego como:
- “Paso”: el jugador no desea subir la apuesta.
- “Igualo, Voy”: el jugador sigue la apuesta máxima y coloca sus fichas en la mesa.
- “Me retiro”: Se retira de la Mano y no se le preguntará nada hasta la próxima Mano.

DEAL_AI | 14
- “Abandono”: Abandona la mesa y ya no se le tendrá más cuenta en el juego.
- “Cambio a la alta/baja”: El jugador coloca sus fichas en su área de cambio según si desea cambio a valores altos o bajos. Implementado por el Modulo de Cambio.
- Preguntas de estado: Se le puede preguntar al sistema información sobre el estado del juego:
Ej: “Dealer actual?”, “Ronda actual?, “Quién es la ciega grande?”, “Apuesta máxima?”…

Cuando se ha llegado a la última Ronda de una Mano el sistema dice a los jugadores que han permanecido al final de la Mano que muestren sus cartas. El sistema reconoce todas las cartas que hay en la mesa gracias al módulo de visión por computador y determina el jugador que ha ganado y la combinación de cartas con lo que lo ha hecho.

Para las siguientes Manos el sistema de juego es el mismo. Se termina el juego cuando solo queda un jugador en la mesa.

DEAL_AI | 15

Módulo de cambio:

Módulo que controla el sistema de cambio de fichas. Se implementa en 3 etapas: reconocimiento de las fichas que se desean cambiar y llevarlas a la banca, tratamiento del valor total de las fichas para establecer cuantas monedas y de qué tipo ha de devolver y por último la secuencia de movimientos para colocar las fichas de cambio.

Funciones:
- recogerFichasMonton(area): Por medio de un área establecida controla el módulo de visión por computador de las fichas para poder reconocerlas y luego a través de las funciones de cinemática inversa coloca esas fichas en su determinada posición de la banca.
- cambiar_fichas_greedy(suma_fichas,mode): Algoritmo greedy (sacado de la asignatura de la mención de Computación “Analisis y disseny d’algortimes” ) implementado para saber qué fichas ha de devolver el robot. Incorpora 2 modos para devolver fichas con valores bajos o máximos.
- dar_Cambio(cambio, q): Recibe qué fichas se han de devolver y la matriz de la posición donde el jugador dejó sus fichas de cambio.

Interacción Robot-Jugador
El sistema es capaz de escuchar (mediante speech-recognition) y contestar (mediante gTTS y playsound). En el apartado de “Jugadores” se darán más detalles sobre este módulo.

Controladores: Esta estructura es la que nos hace de puente entre todos los módulos existentes y nos permite la transmisión de entradas (inputs) y salidas (outputs) a sus respectivos módulos.

Todo y que los controladores en el diseño van como un módulo a parte, se ha decidido finalmente unificarlos junto a los principales ficheros como el main, speakAndListen etc…

DEAL_AI | 16

### Jugadores:

Representa el colectivo de seres humanos que están realizando una partida con el Deal AI. Estos son los que generarán los inputs principales, los cuales determinarán al robot qué algoritmo utilizar y con qué módulos operar.

En cuanto a este módulo, se han implementado unas funciones de interacción robot-humano. Se han usado los módulos/librerías speech_recognition (para el reconocimiento de voz, así dando la oportunidad de controlar las acciones del robot), gTTS (para poder leer con voz sintética (text-to-speech) las respuestas dadas por el robot) y playsound (para poder reproducir sonidos y poder leer los resultados obtenidos por el gTTS).

DEAL_AI | 17

Amazing contributions

Deal AI cuenta con las siguientes funciones:

- Seguimiento automático de una partida en vivo de póker texas holdem.
- Repartición de cartas a los jugadores.
- Volteo de cartas automático.
- Intercambio de fichas mediante algoritmos greedy.
- Colocación de cartas compartidas mediante visión por computador.
- Explicación de la situación actual mediante voz (text to speech).
- Avance de la partida mediante comandos de voz.
- Resolución de preguntas básicas mediante el módulo de sonido.
- Reacción ante importunos.

En caso de realizar todos y cada uno de los objetivos creemos que la nota debería equivaler a un excelente. La máxima nota podría ser obtenida dependiendo de la eficiencia del robot ante las situaciones mencionadas anteriormente.

Componentes y piezas 3D extras

■ Brazo

■ Soporte cámara

■ Pieza “flip” de cartas

■ Pieza contenedora de fichas

■ Soporte cartas

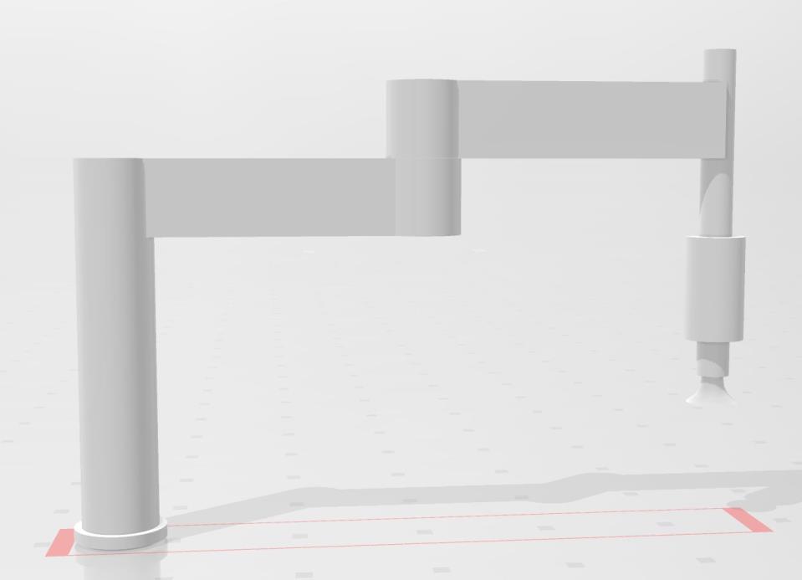
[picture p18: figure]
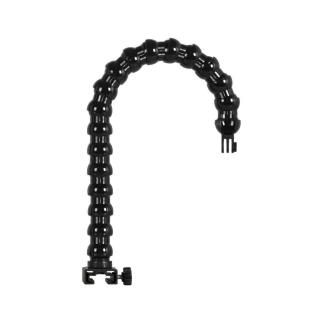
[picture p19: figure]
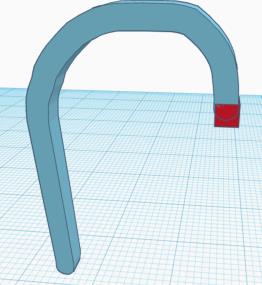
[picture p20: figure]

DEAL_AI | 18
1) Brazo: | Componentes unidos del brazo robótico (total de 4 piezas por
separado).
2) Soporte de cámara: Pieza que sostiene la cámara de tal modo que nos permite obtener una vista cenital de la mesa así evitando el ser tapada por el propio brazo y consiguiendo un sistema de cálculos más simple.

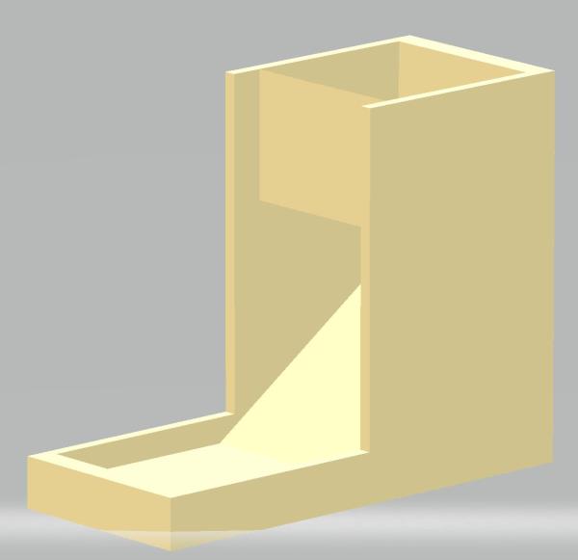
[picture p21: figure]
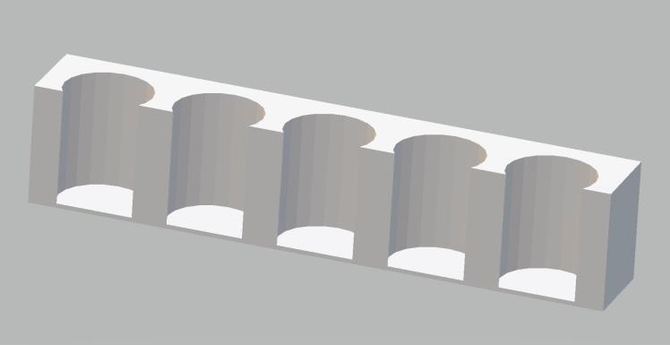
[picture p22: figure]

DEAL_AI | 19
3) Pieza “flip” de cartas: Pieza con dos conductos que, al introducir una carta por ésta, le da la vuelta y la expulsa por el otro conducto. De este modo conseguimos un “flip” automático de las cartas haciendo el robot independiente para esta tarea. La carta termina en una badeja y De este modo podemos tener en todo momento controlada la carta.
4) Contenedor de fichas: Pieza estática que nos facilitará el proceso de clasificación de fichas y además, servirá de contenedor.

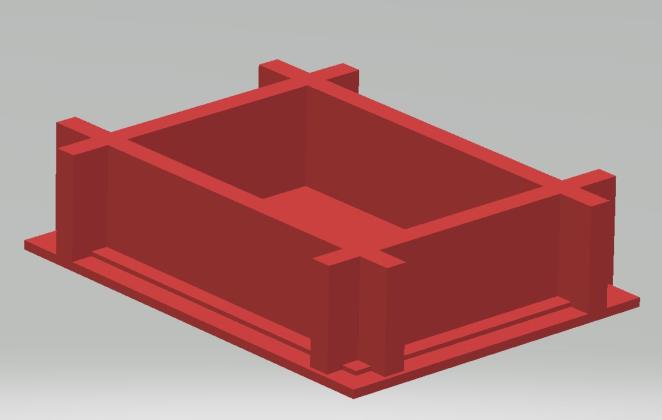
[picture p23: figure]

DEAL_AI | 20
5) Soporte cartas: Pieza sencilla que nos servirá como soporte para la baraja. De este modo aseguramos que la baraja se mantiene estática en un lugar y no se desmonta al coger una carta.

Se ha decidido hacer el modelo simple de los propuestos en el primer sprint, siguiendo los siguientes razonamientos: Teniendo en cuenta que la dimensión de una carta es de 64mm x 88mm, el hueco interno del soporte de las cartas se ha ampliado en 1'5mm para cada uno de los 4 lados, estableciendo pues un hueco interior de 67mm x 91mm, así pues, hemos decidido que el ancho de cada pared del receptáculo sea de 4.5mm, el resultado final es este, una pequeña caja sin tapa de dimensiones 76mm x 100mm x 25mm (suponiendo que una baraja de cartas tenga un tamaño máximo de 20mm de altura, así pues dejamos 5mm como margen).

DEAL_AI | 21

Estrategia de simulación

La estrategia de simulación que seguiremos será la de ofrecer una simulación de una partida real y en vivo, mostrando en ésta todas las funcionalidades descritas en los apartados anteriores. De este modo podremos demostrar la funcionalidad real de nuestro robot además de mostrar que en un caso práctico real da la talla, es decir, cumple todas las funcionalidades presentadas.

En cuanto al sistema o simuladores que usaremos, este va a ser CoppeliaSim ya que lo estamos aprendiendo a usar en las clases de problemas, nos sirve perfectamente para nuestro robot y además, se puede enlazar con Python que será el lenguaje que usaremos para programar los módulos de detección de sonido, visión por computador, la propia simulación de la partida etc…

Los módulos simulados dentro de la partida serán las principales funcionalidades mencionadas en los apartados anteriores.

De las primeras simulaciones hemos obtenido los siguientes resultados y conclusiones:

Las simulaciones sobre el módulo de voz han sido satisfactorias. Se han detectado correctamente las “key words” en varias pruebas que hemos hecho con distintos sujetos.

De las simulaciones generales no han habido resultados satisfactorios debido a ciertos factores: primero, el modelo que tenemos de carta hace movimientos raros que no entendemos (sale volando sin sentido, sin ser tocada, lo hace de forma automática) y debemos preguntar al tutor. El otro problema encontrado es que el brazo hace movimientos no coherentes cuando le enviamos a un punto, cosa que nos ha hecho llegar a la conclusión que cierta parte del código de cinemática inversa está erróneo.

DEAL_AI | 22

Simulaciones para módulo de Visión por computador:

Inicialmente, se hicieron pruebas con imágenes con 1 o mas cartas sin ningún tipo de inclinación y con resoluciones bajas (512x256), esto causaba varios problemas:

- La cámara está bastante elevada y cada carta ocupa unos pocos píxeles, lo que hacía imposible reconocer tanto los valores como el tipo de la carta.
- Al no tener inclinación las cartas, hacía que los casos probados no fuesen realistas ya que un jugador no porqué dejar la carta encima de la mesa totalmente recta.
- Algunos parámetros dependían de la resolución, lo que si en un futuro se quiere cambiar solo la cámara resultaría un problema. Esto también tenía repercusión en algunas partes del código donde en futuras simulaciones con cartas con inclinación hacía que saltasen errores.

En posteriores simulaciones con cartas con inclinación, donde se aumentó la resolución de la cámara (1024x512) y se cambiaron parámetros para que escalasen con la resolución. Finalmente obtuvimos los resultados que esperábamos, detectaba los valores y tipos de cartas con un porcentaje de acierto muy alto y decía quién era el ganador sin ningún tipo de problema.

Simulaciones cinemática inversa:

En cuanto al sistema de repartir y manipular cartas, nuestro grupo se encuentra con un problema relacionado con las físicas del simulador que no ha sido capaz de solventar. Se ha buscado una solución para casi todos los apartados en los que ocasionaba error, pero en el módulo de dar la vuelta a las cartas no se ha podido encontrar una manera real de hacerlo, por tanto, no hemos tenido éxito simulándolo.

DEAL_AI | 23

No obstante, se ha llevado a cabo la simulación y comprobación de los módulos básicos de manipulación de cartas y estos han sido los resultados:

- Gestión correcta de una partida de entre 2 y 5 jugadores.
- Es capaz de revelar las 5 cartas correctamente e incluso puede revelar hasta un total de 7 cartas sin obstruir la zona de juego (aplicable para otras modalidades de póker).
- Buena compenetración entre los distintos módulos de gestión de cartas.
- Cálculo computacional de las ecuaciones rápido.

Sin embargo, un problema que hemos encontrado es la diferencia de tiempos entre la ejecución de código y el simulador. Al ejecutar, concretamente, una función de espera (en nuestro caso, de la librería time, time.sleep(segundos)) empieza a contar los segundos de espera desde que es ejecutada y utiliza como referencia el tiempo real. Esto, al intentarlo sincronizar con la ejecución, nos es un problema debido que la velocidad de ejecución del simulador (sus frames por segundo), depende de la capacidad del ordenador, por tanto, si no se dispone de un ordenador con buenos recursos, los tiempos no irán sincronizados, pues si un movimiento del robot tarda 1 segundo para ir de un punto a otro en 60fps, tardará el doble si va a 30fps y, como el tiempo de espera depende del tiempo del ordenador y no el de la ejecución, significa que se han de colocar tiempos mayores y, por consecuencia, esperas más elevadas en ordenadores que tienen peores recursos. En nuestro caso nuestra media de fps rondaba los 13.

DEAL_AI | 24

Posibles riesgos y plan de contingencia

Risk # | Description | Probability (High/Medium/Low) | Impact (High/Medium/Low) | Contingency plan
1 | Que la superficie de la ficha no sea completamente plana y la válvula de vacío no coja correctamente la ficha | Low | High | 1- Utilizar fichas personalizadas 2- Válvula con más potencia
2 | Válvula sin potencia para coger fichas (al levantarlas caen por su propio peso) | Low | High | Cambiar válvula
3 | Giros bruscos hacen caer las fichas y / o cartas | Medium | Medium | 1-Movimientos más lentos 2- Reducir el movimiento al llegar al punto de destino
4 | Cartas se doblan debido a que las personas tienen contacto con ellas y hace que la válvula no las coja correctamente | Medium | Medium | Utilizar válvula con más potencia
5 | Relacionado con el punto 4: las cartas se doblan y como consecuencia el aparato de darle la vuelta a las cartas deja de funcionar | Low | High | Cambiar diseño aparato que le da la vuelta a las cartas
6 | Confundir ficha con algún decorado de la mesa | Low | Medium | Poner un manto para aumentar contraste
7 | Que al dejar las fichas en la caja, reboten y se salgan como consecuència | Low | Low | Ajustar distancia con sensores

DEAL_AI | 25

## Referencias

Este Proyecto ha estado inspirado por los siguientes proyectos de internet:

#1 https://github.com/OriolMoreno/C.A.R.L.E.S

#2 https://www.banggood.com/DIY-4DOF-Pump-RC-Robot-Arm-Educational-Kit-With-Metal-Digital-Servo-For-Arduino-p-1424994.html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 (https://www.banggood.com/DIY-4DOF-Pump-RC-Robot-Arm-Educational-Kit-With-Metal-Digital-Servo-For-Arduino-p-1424994.html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)

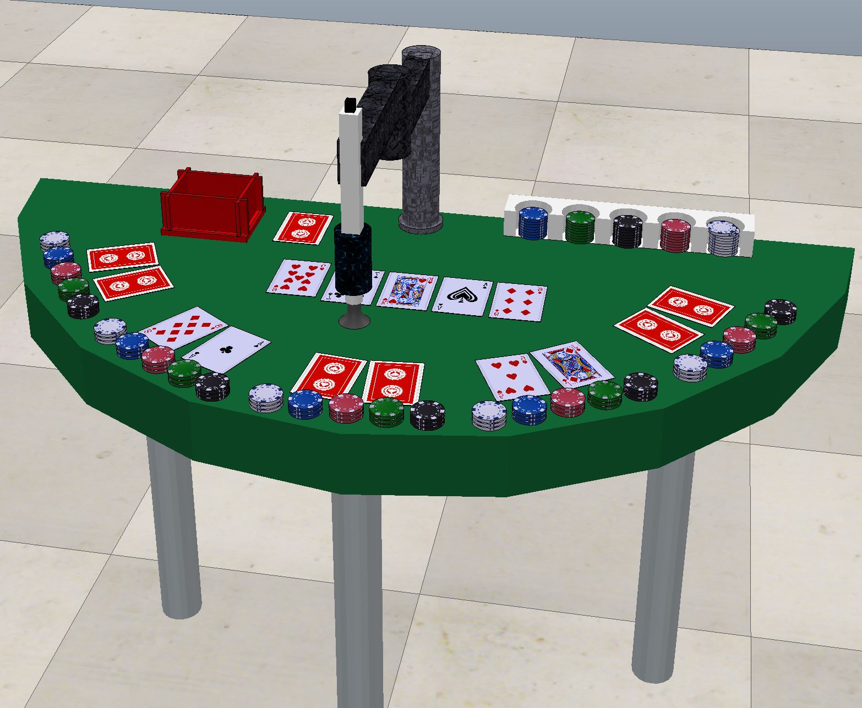
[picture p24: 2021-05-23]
img/foto_dealAI.JPG

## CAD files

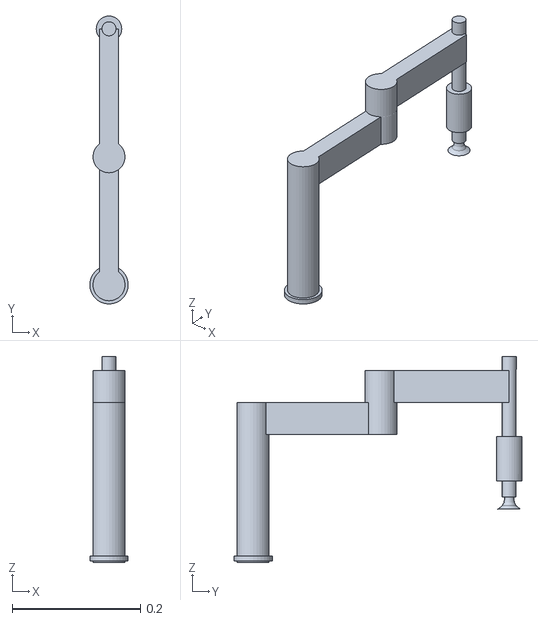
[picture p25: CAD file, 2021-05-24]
Objetos STL/Brazo.stl
0.06 x 0.45 x 0.322

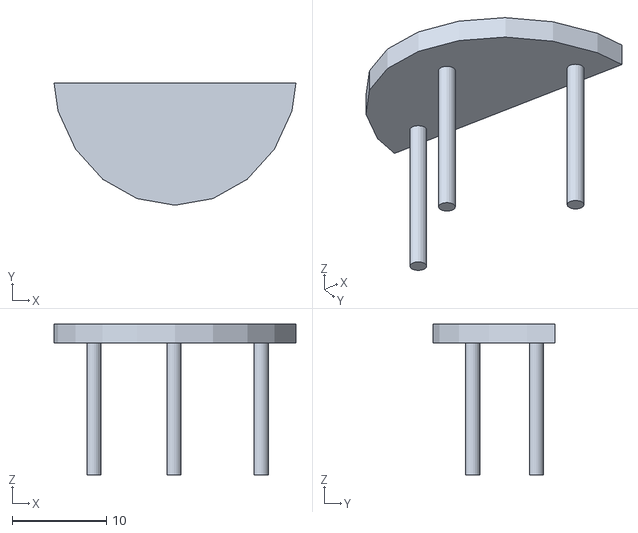
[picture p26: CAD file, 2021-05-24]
Objetos STL/Mesa.stl
25.7 x 13.0 x 16.0

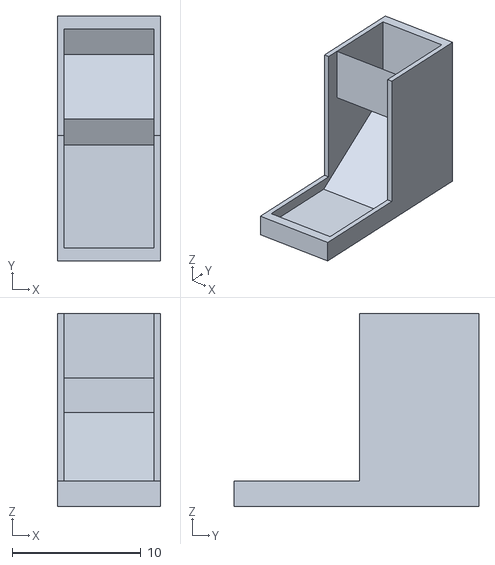
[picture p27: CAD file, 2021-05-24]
Objetos STL/Flipeador.stl
8.00 x 19.0 x 15.0

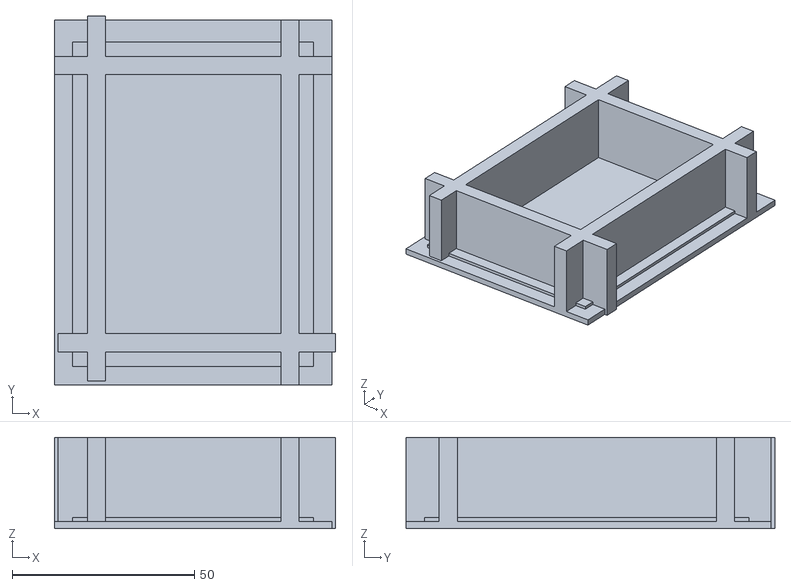
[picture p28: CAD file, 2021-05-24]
Objetos STL/base_cartas.stl
77.0 x 101.0 x 25.0

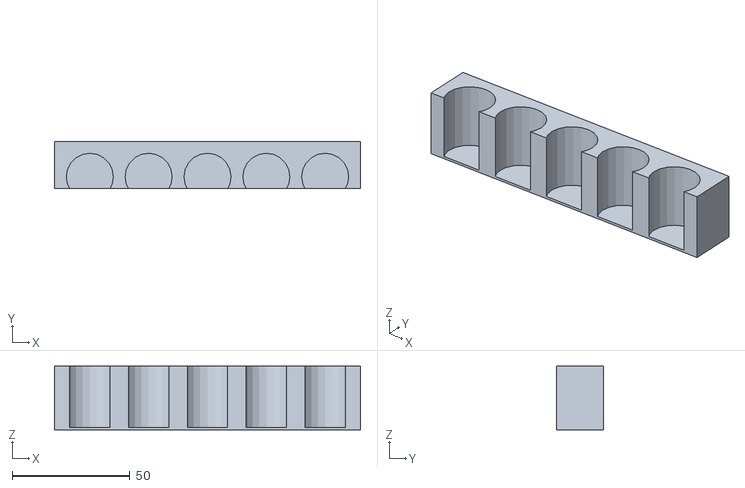
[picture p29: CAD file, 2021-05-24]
Objetos STL/sujetafichas.stl
130.0 x 20.0 x 27.0

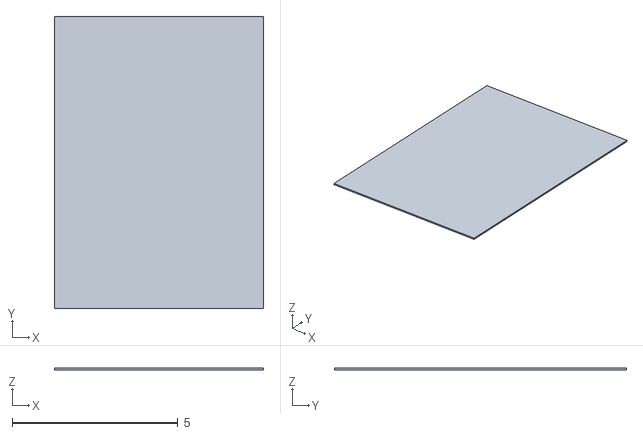
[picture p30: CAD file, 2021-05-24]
Objetos STL/Carta.stl
6.30 x 8.80 x 0.05

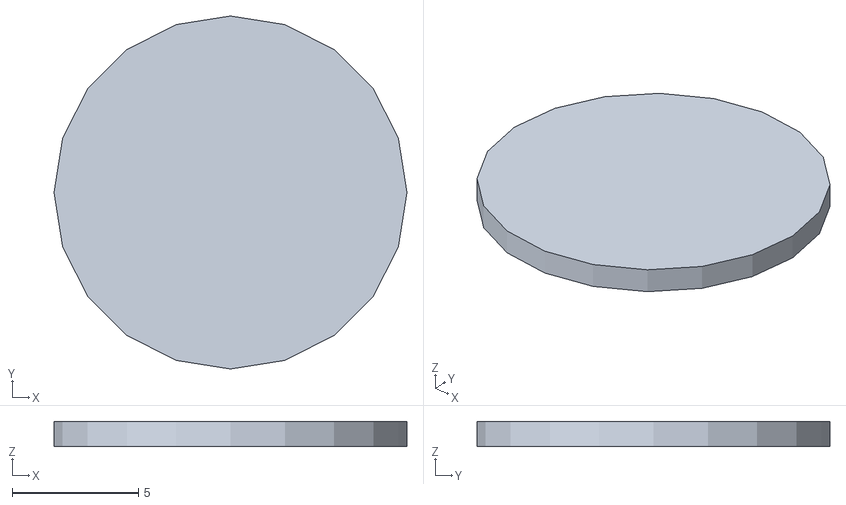
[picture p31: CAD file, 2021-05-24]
Objetos STL/Ficha.stl
14.0 x 14.0 x 1.00

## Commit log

2021-05-24 Objetos escena
    [Brazo.stl, Carta.stl, Ficha.stl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]
2021-05-24 gif de proceso de detección de fichas
2021-05-24 Actualizacion de v2
    Código más general. Se han añadido preguntas de estado. Falta unir con Flipeador
2021-05-26 Escena Coppelia para hasta 5 jugadores
